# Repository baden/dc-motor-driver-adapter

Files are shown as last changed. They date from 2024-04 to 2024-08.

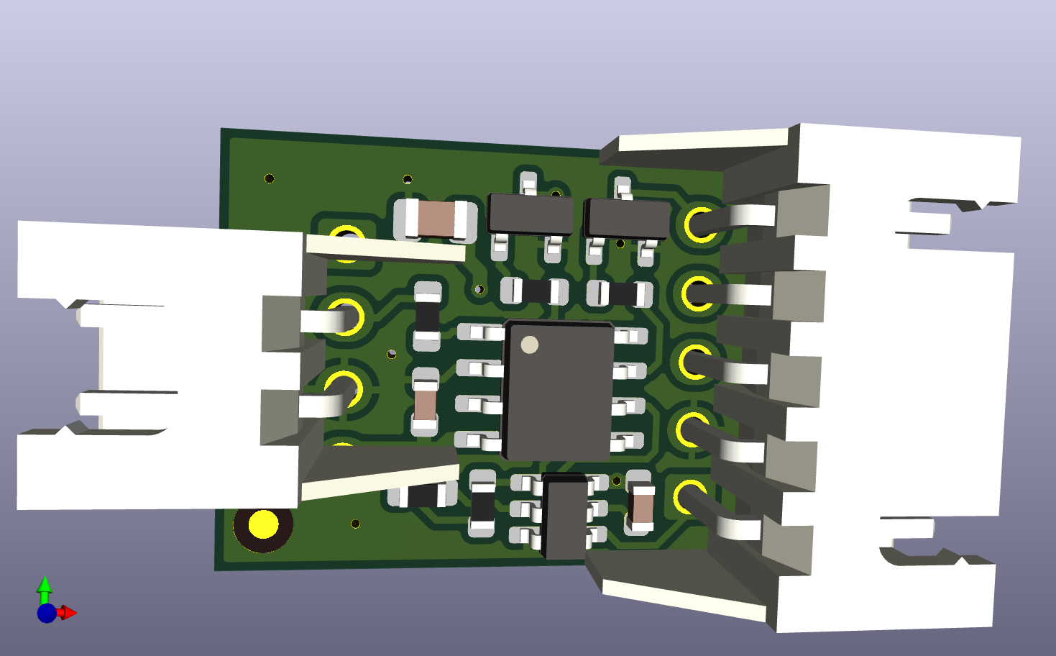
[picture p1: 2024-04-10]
board/revision-3/docs/dc-motor-driver-adapter.png

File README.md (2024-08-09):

# dc-motor-driver-adapter

Тут буде і плата і програма.

## Встановлення інструментів

https://github.com/riscv-software-src/homebrew-riscv

```bash
brew tap riscv-software-src/riscv
brew install riscv-tools
brew install riscv-openocd
brew test riscv-tools
/opt/homebrew/opt/riscv-gnu-toolchain/bin/riscv64-unknown-elf-gcc --version
```

/opt/homebrew/opt/riscv-openocd/bin/openocd

Во, подивиться це:

https://github.com/wagiminator/CH32V003-GameConsole/tree/main

Ще це:
https://github.com/wagiminator/MCU-Templates

Ще тут купа посилань:
https://github.com/wagiminator/Development-Boards/tree/main/CH32V003A4M6_DevBoard

https://github.com/AlessandroAU/ESP32-CRSF-Packet-Gen/blob/master/CRSF_testcode/CRSF.h
https://px4.github.io/Firmware-Doxygen/d9/dd2/crsf_8cpp_source.html

https://github.com/vedderb/bldc_uart_comm_stm32f4_discovery/blob/c19a6283e187040f25aa52e213673938db054d06/bldc_interface.c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

https://vedder.se/2015/10/communicating-with-the-vesc-using-uart/

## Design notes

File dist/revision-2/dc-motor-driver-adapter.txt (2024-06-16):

Name: dc-motor-driver-adapter
Revision: 2

Dimension: 16.0mm x 10.0mm
Thickness: 1.6mm
Layers: 2

Gerber files:

Copper layers (orger from top to bottom):
Top copper:         dc-motor-driver-adapter-F_Cu.gtl
Bottom copper:      dc-motor-driver-adapter-B_Cu.gbl

Top solder mask:    dc-motor-driver-adapter-F_Mask.gts
Bottom solder mask: dc-motor-driver-adapter-B_Mask.gbs
Silkscreen:         dc-motor-driver-adapter-B_Silkscreen.gbo
Outline:            dc-motor-driver-adapter-Edge_Cuts.gm1
Top solder paste:   dc-motor-driver-adapter-F_Paste.gtp
Drill:              dc-motor-driver-adapter.drl

Color of solder mask: green
Silkscreen color: white
Surface Finish: HASL

Copper weight: 1oz

Material details: FR4-Standard Tg 140C

Recomend panelizing: 4x5 vcut

Components positions: dc-motor-driver-adapter-top.pos
Components positions (CSV): dc-motor-driver-adapter-top.pos.csv
Components positions (human pdf): dc-motor-driver-adapter-Top.pdf
Components positions (human pdf): dc-motor-driver-adapter-Bottom.pdf

Components list: dc-motor-driver-adapter.bom.csv

Assembled board example: dc-motor-driver-adapter.png

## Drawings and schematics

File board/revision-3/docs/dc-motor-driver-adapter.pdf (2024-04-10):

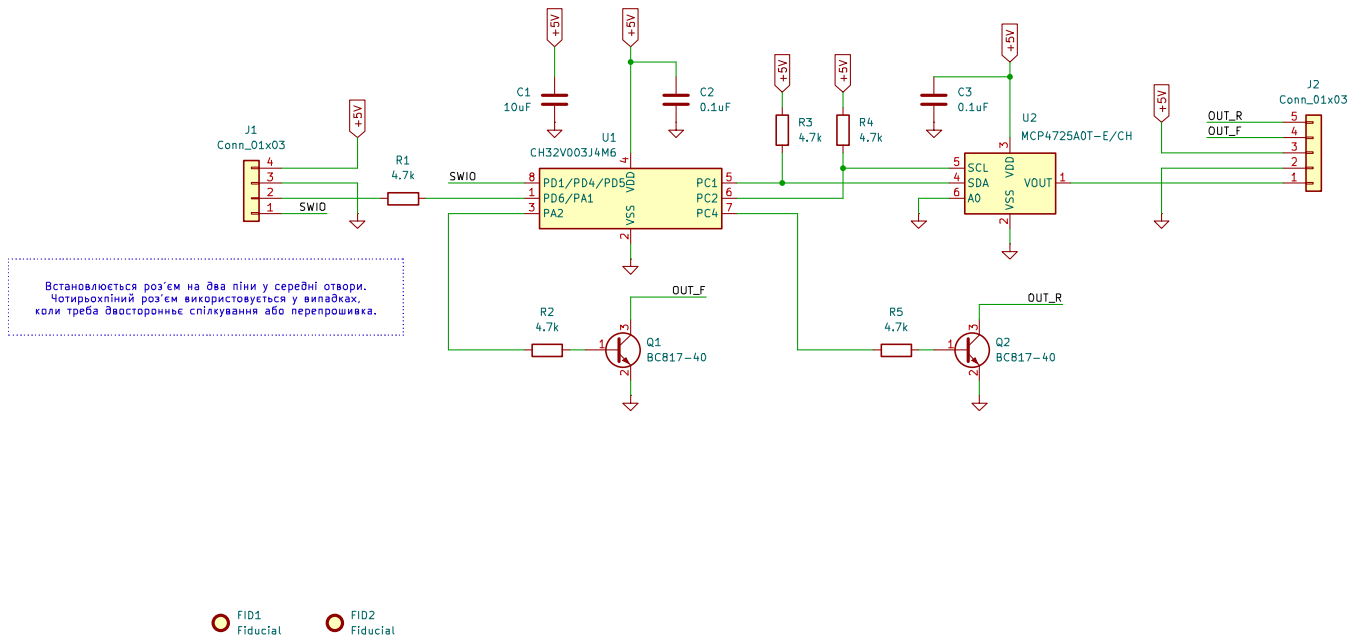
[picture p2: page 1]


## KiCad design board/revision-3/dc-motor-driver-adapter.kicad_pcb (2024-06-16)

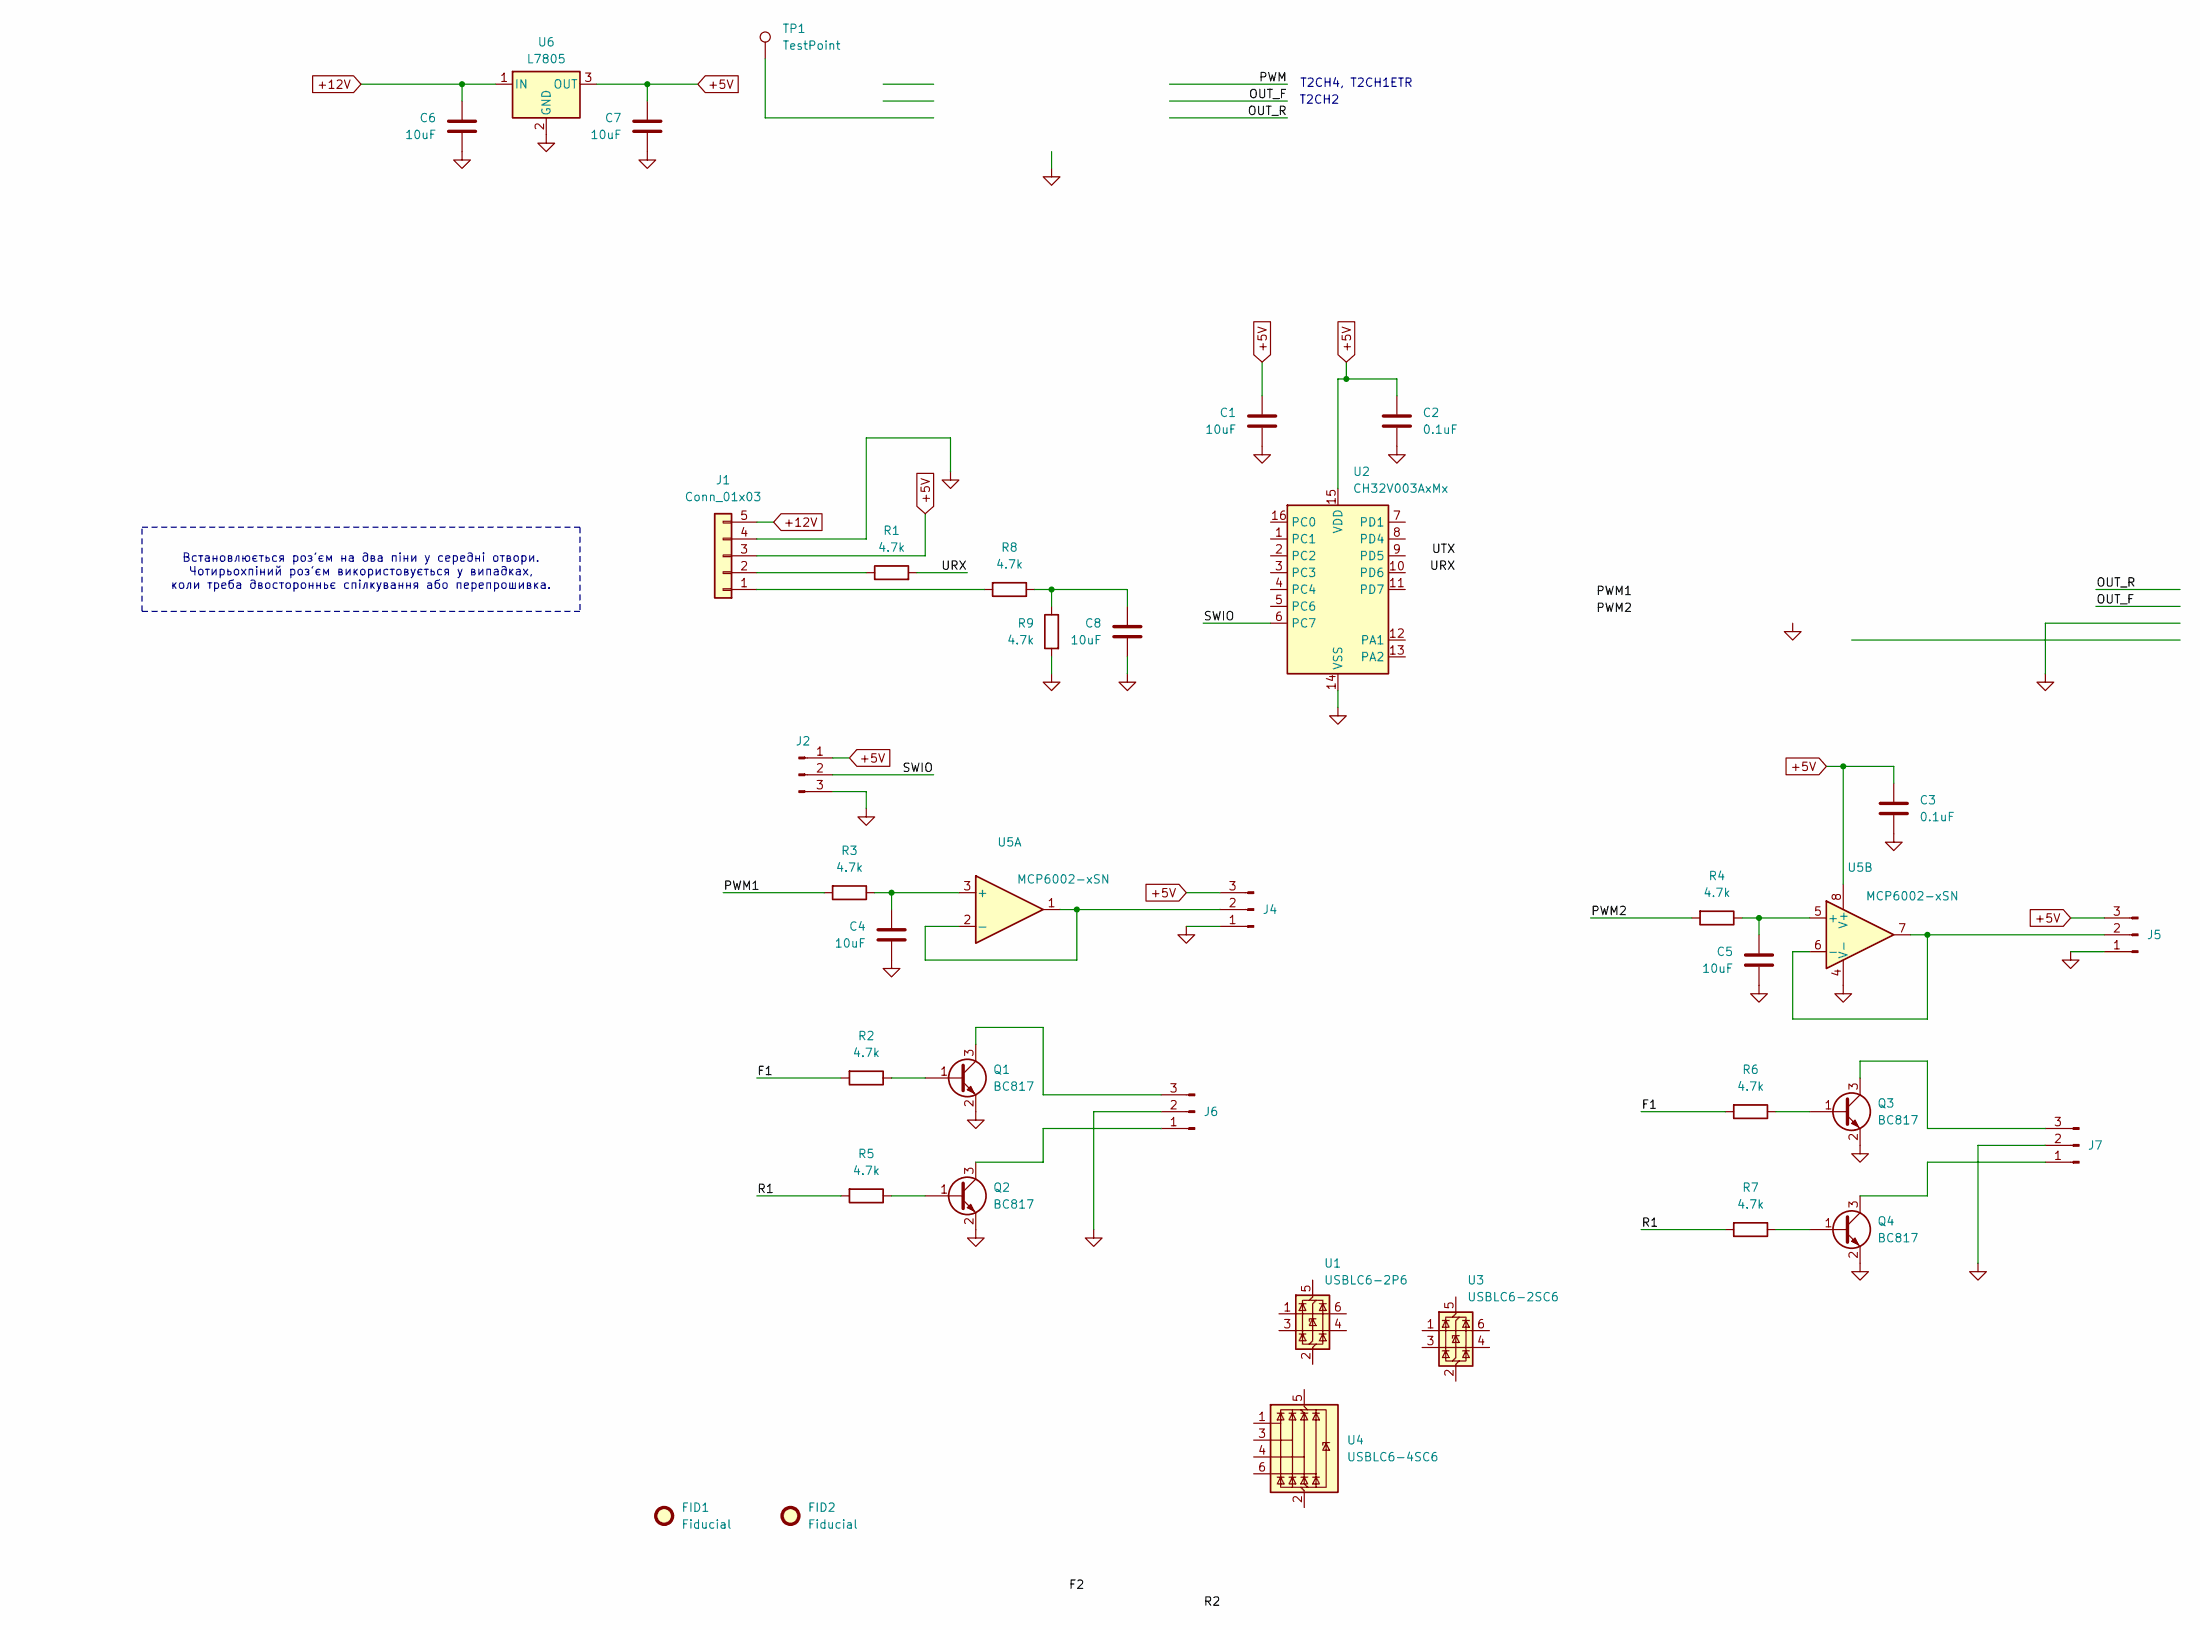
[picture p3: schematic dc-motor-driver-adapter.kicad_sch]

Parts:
C1, C4, C5, C6, C7, C8: 10uF; C_0805_2012Metric
C2, C3: 0.1uF; C_0603_1608Metric
FID1, FID2: Fiducial; Fiducial_1mm_Mask2mm
J1: Conn_01x03; JST_PH_S5B-PH-K_1x05_P2.00mm_Horizontal
J2, J4, J5, J6, J7: Conn_01x03_Pin; JST_PH_B3B-PH-K_1x03_P2.00mm_Vertical
Q1, Q2, Q3, Q4: BC817; SOT-23
R1, R2, R3, R4, R5, R6, R7, R8, R9: 4.7k; R_0603_1608Metric
TP1: TestPoint; TestPoint_Pad_2.0x2.0mm
U1: USBLC6-2P6; SOT-666
U2: CH32V003AxMx; SOP-16_3.9x9.9mm_P1.27mm
U3: USBLC6-2SC6; SOT-23-6
U4: USBLC6-4SC6; SOT-23-6
U5: MCP6002-xSN; SO-8_3.9x4.9mm_P1.27mm
U6: L7805; TO-252-2

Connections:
+5V: C1.1, C2.1, C3.1, C7.1, J1.3, J2.1, J4.3, J5.3, U2.15 (VDD), U5.8 (V+), U6.3 (OUT)
+12V: C6.1, J1.5, U6.1 (IN)
/F1: R2.2, R6.2
/PWM1: R3.2
/PWM2: R4.2
/R1: R5.2, R7.2
/SWIO: J2.2, U2.6 (PC7)
/URX: R1.2
GND: C1.2, C2.2, C3.2, C4.2, C5.2, C6.2, C7.2, C8.2, J1.4, J2.3, J4.1, J5.1, J6.2, J7.2, Q1.2 (E), Q2.2 (E), Q3.2 (E), Q4.2 (E), R9.2, U2.14 (VSS), U5.4 (V-), U6.2 (GND)
unnamed: C8.1, R8.1, R9.1
unnamed: J1.2, R1.1
unnamed: J4.2, U5.1, U5.2 (-)
unnamed: J5.2, U5.6 (-), U5.7
unnamed: J6.1, Q2.3 (C)
unnamed: J6.3, Q1.3 (C)
unnamed: J7.1, Q4.3 (C)
unnamed: J7.3, Q3.3 (C)
unnamed: Q1.1 (B), R2.1
unnamed: Q2.1 (B), R5.1
unnamed: Q3.1 (B), R6.1
unnamed: Q4.1 (B), R7.1
unnamed: J1.1, R8.2
unnamed: C4.1, R3.1, U5.3 (+)
unnamed: C5.1, R4.1, U5.5 (+)

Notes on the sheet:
Встановлюється роз'єм на два піни у середні отвори. Чотирьохпіний роз'єм використовується у випадках, коли треба двосторонньє спілкування або перепрошивка.
T2CH2
T2CH4, T2CH1ETR

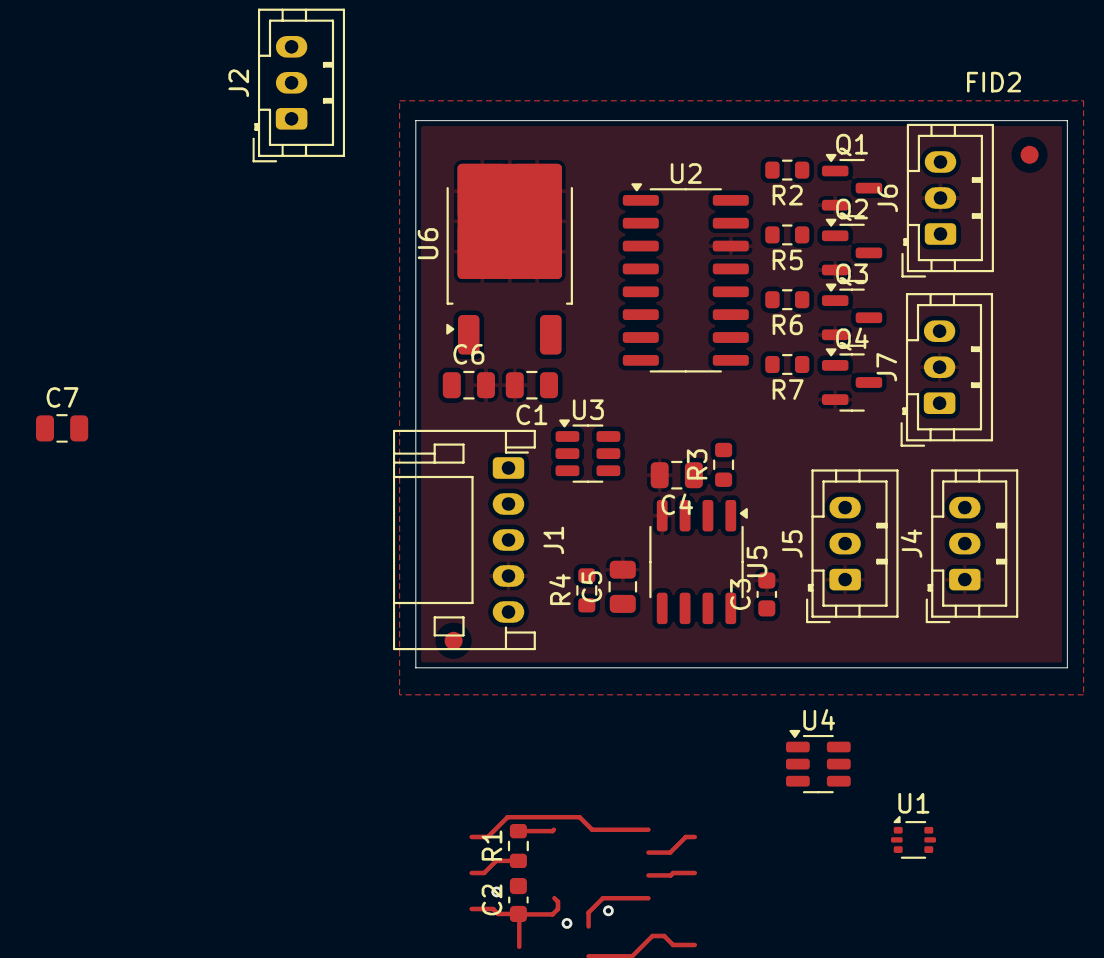
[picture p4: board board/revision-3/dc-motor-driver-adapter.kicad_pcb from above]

Board: 2 copper layers, 36.2 x 30.4 mm, 33 parts (1 on the bottom side), 19 nets.

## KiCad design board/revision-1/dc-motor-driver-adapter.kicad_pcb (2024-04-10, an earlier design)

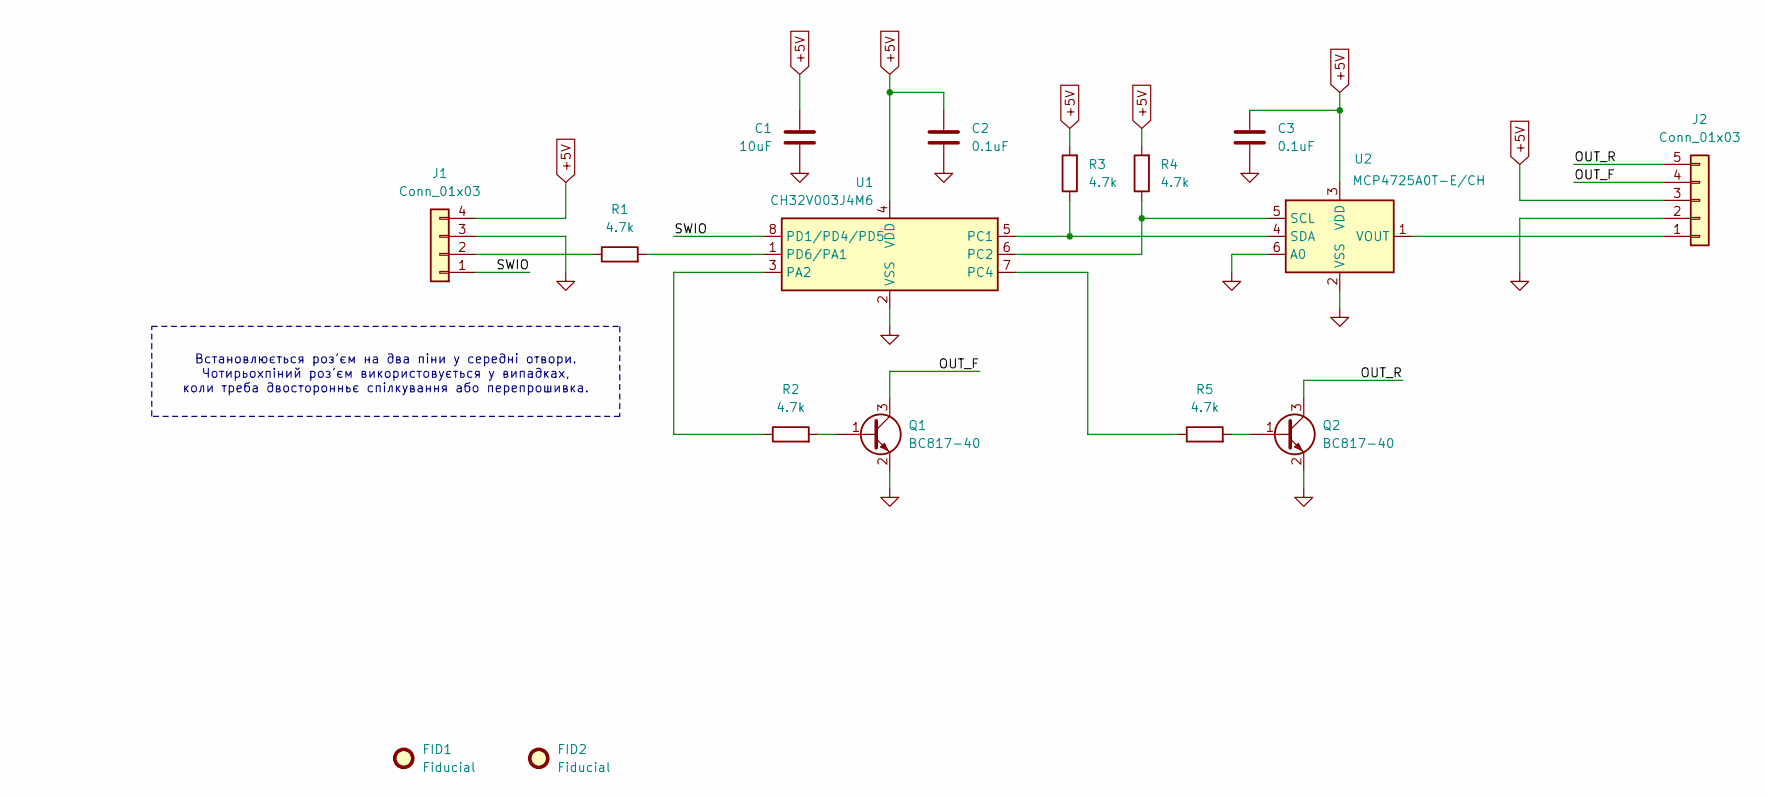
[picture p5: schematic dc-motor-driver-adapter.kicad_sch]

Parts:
C1: 10uF; C_0805_2012Metric
C2, C3: 0.1uF; C_0603_1608Metric
FID1, FID2: Fiducial; Fiducial_1mm_Mask2mm
J1: Conn_01x03; JST_XH_S4B-XH-A-1_1x04_P2.50mm_Horizontal
J2: Conn_01x03; JST_XH_S5B-XH-A-1_1x05_P2.50mm_Horizontal
Q1, Q2: BC817-40; SOT-23
R1, R2, R3, R4, R5: 4.7k; R_0603_1608Metric
U1: CH32V003J4M6; SOP-8_3.9x4.9mm_P1.27mm
U2: MCP4725A0T-E/CH; SOT-23-6

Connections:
+5V: C1.1, C2.1, C3.1, J1.4, J2.3, R3.2, R4.2, U1.4 (VDD), U2.3 (VDD)
/OUT_F: J2.4, Q1.3 (C)
/OUT_R: J2.5, Q2.3 (C)
/SWIO: J1.1, U1.8 (PD1/PD4/PD5)
GND: C1.2, C2.2, C3.2, J1.3, J2.2, Q1.2 (E), Q2.2 (E), U1.2 (VSS), U2.2 (VSS), U2.6 (A0)
unnamed: J1.2, R1.1
unnamed: J2.1, U2.1 (VOUT)
unnamed: Q1.1 (B), R2.2
unnamed: Q2.1 (B), R5.2
unnamed: R2.1, U1.3 (PA2)
unnamed: R3.1, U1.5 (PC1), U2.4 (SDA)
unnamed: R4.1, U1.6 (PC2), U2.5 (SCL)
unnamed: R5.1, U1.7 (PC4)
unnamed: R1.2, U1.1 (PD6/PA1)

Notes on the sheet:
Встановлюється роз'єм на два піни у середні отвори. Чотирьохпіний роз'єм використовується у випадках, коли треба двосторонньє спілкування або перепрошивка.

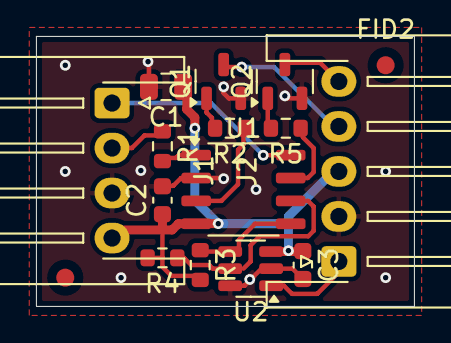
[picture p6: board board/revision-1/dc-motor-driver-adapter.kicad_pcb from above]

Board: 2 copper layers, 21.0 x 15.0 mm, 16 parts (0 on the bottom side), 14 nets.

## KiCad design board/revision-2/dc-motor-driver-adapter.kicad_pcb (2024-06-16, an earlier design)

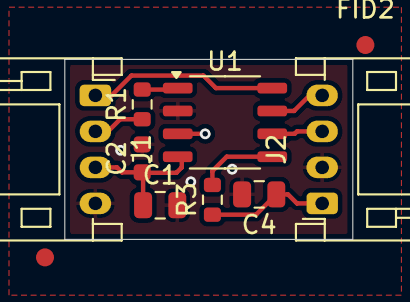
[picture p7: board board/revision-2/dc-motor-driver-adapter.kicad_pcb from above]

Board: 2 copper layers, 16.0 x 10.0 mm, 11 parts (1 on the bottom side), 10 nets.

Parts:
C1, C4: 10uF; C_0805_2012Metric
C2: 0.1uF; C_0603_1608Metric
FID1, FID2: Fiducial; Fiducial_1mm_Mask2mm
J1, J2: Conn_01x03; JST_PH_S4B-PH-K_1x04_P2.00mm_Horizontal
R1, R3: 4.7k; R_0603_1608Metric
TP1: TestPoint; TestPoint_Pad_2.0x2.0mm
U1: CH32V003J4M6; SOP-8_3.9x4.9mm_P1.27mm

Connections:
+5V: C1.1, C2.1, J1.3, U1.4 (VDD)
/OUT_F: J2.3, U1.6 (PC2)
/OUT_R: J2.4, U1.7 (PC4)
/PWM: R3.2, U1.5 (PC1)
/SWIO: J1.1, U1.8 (PD1/PD4/PD5)
/URX: R1.2, U1.1 (PD6/PA1)
GND: C1.2, C2.2, C4.2, J1.4, J2.2, U1.2 (VSS)
unnamed: J1.2, R1.1
unnamed: C4.1, J2.1, R3.1
unnamed: TP1.1, U1.3 (PA2)

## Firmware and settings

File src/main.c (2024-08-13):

#include <stdbool.h>
#include "gpio.h"
#include "debug_serial.h"
#include "uart_rx.h"
#include "crsf.h"
#include "dac.h"
#include "system.h"


// Device modes:
// 1 - Керування лебідкою по каналу 12
// 2 - Керування лівим бортом по каналах 1 та 2  (1+2)
// 3 - Керування правим бортом по каналах 1 та 2 (2-1)

#if !defined(DEVICE_MODE)
    #error "DEVICE_MODE is not defined"
#endif
// #define DEVICE_MODE 3

// Керування тільки аналоговим виходом з нулем у середині діапазону
#define DEVICE_ANALOG_ONLY 1

//#define STARTKIT 1

#if defined(STARTKIT)

    #define PIN_LED    PD0   // pin connected to LED (Startkit)

#else

#endif


static inline void init(void)
{
    #if defined(STARTKIT)
        PIN_output(PIN_LED);
        PIN_high(PIN_LED);

        PIN_output(PC0);   // "+" for LED
        PIN_high(PC0);
    #endif

    #if 0
    PIN_input_PD(PD6); // Вхід для PPM (UART) (підтягнутий до землі)
    #endif

    // SYS_init();
    UART_init();
    dac_init();

    #if DEVICE_MODE == 1
        dac_write(2730);        // TODO: Підібрати напругу 12В
    #else
        #if defined(DEVICE_ANALOG_ONLY) && (DEVICE_ANALOG_ONLY == 1)
            dac_write(2047);    // За замовчуванням напруга 1/2
        #else
            dac_write(4095);
        #endif
    #endif

#if 0
    // Configure PD6 as interrupt input
    // The "port" is:
    // 0 for Port A
    // 1 for Port B
    // 2 for Port C
    // 3 for Port D
    #define _portno 3
    #define _pin 6

    RCC->APB2PCENR |= RCC_AFIOEN;
	// Configure the IO as an interrupt.
    AFIO->EXTICR = _portno << (_pin * 2);
	EXTI->INTENR = EXTI_INTENR_MR6; // Enable EXT6
	EXTI->RTENR = EXTI_RTENR_TR6;  // Rising edge trigger
    EXTI->FTENR = EXTI_FTENR_TR6;  // Falling edge trigger

    // enable pin-change-interrupt.
    NVIC_EnableIRQ( EXTI7_0_IRQn );
#endif

#if 0
    RCC->APB2PCENR |= RCC_TIM1EN; // enable TIM1 clock
    // RCC->APB2PRSTR = RCC_TIM1RST;
	// RCC->APB2PRSTR = 0;

	TIM1->ATRLR = 0xffff;
	TIM1->PSC = 47; // 48MHz/(47+1) -> 1µs resolution

    // D2 Capture Input(T1CH1)
    // PA1 - T1CH2

	TIM1->CHCTLR1 = TIM_CC1S_0 | TIM_CC2S_1;

	TIM1->CCER = TIM_CC1E|TIM_CC2E|TIM_CC2P;

	TIM1->CTLR1 = TIM_CEN;

	NVIC_EnableIRQ(TIM1_CC_IRQn);
	TIM1->DMAINTENR = TIM_CC1IE|TIM_CC2IE;    
#endif

//   ADC_init();
//   ADC_input(PIN_PAD);

    // DEBUG_init();
}

#if 0
volatile unsigned int counter = 0;
volatile uint32_t last_value = 0;

void EXTI7_0_IRQHandler( void ) __attribute__((interrupt));
void EXTI7_0_IRQHandler( void ) 
{
    static uint32_t starttime;

    PIN_high(PC1);
    unsigned pin = PIN_read(PD6);

    if(pin != 0) {
        starttime = STK->CNT;
    } else {
        last_value = STK->CNT - starttime;
    }
	EXTI->INTFR = EXTI_INTF_INTF6;
    PIN_low(PC1);
}
#endif

#if DEVICE_MODE == 1

static void rxTo(int val)
{
    if(val < 500) {
        #if defined(STARTKIT)
            PIN_low(PIN_LED);
        #endif
        PIN_high(PC4);
        PIN_low(PA2);
    } else if(val > 1500) {
        #if defined(STARTKIT)
            PIN_low(PIN_LED);
        #endif
        PIN_low(PC4);
        PIN_high(PA2);
    } else {
        #if defined(STARTKIT)
            PIN_high(PIN_LED);
        #endif
        PIN_low(PC4);
        PIN_low(PA2);
    }
}

static void rxFoo()
{
    int val = channel[12 -1];

    // Middle = 1044
    // Low = 191
    // High = 1792
    rxTo(val);
}

#elif (DEVICE_MODE == 2) || (DEVICE_MODE == 3) 

#define LOW_PASS_FILTER
// CRSF center value is 992
#define CENTER_X 992
#define CENTER_Y 992
#define MAX_X 820
#define MAX_Y 820
#define DEAD_ZONE 10

static void rxTo(int dac_val)
{
    #ifdef LOW_PASS_FILTER
        static int last_dac_val = 0;
        int _dac = dac_val;
        dac_val = (dac_val + last_dac_val) / 2;
        last_dac_val = _dac;
    #endif

    if((dac_val < DEAD_ZONE) && (dac_val > -DEAD_ZONE)) {
        #if defined(DEVICE_ANALOG_ONLY) && (DEVICE_ANALOG_ONLY == 1)
            dac_write(2047);
        #else
            dac_write(4095);
            PIN_low(PC4);
            PIN_low(PA2);
        #endif
    } else {
        #if defined(DEVICE_ANALOG_ONLY) && (DEVICE_ANALOG_ONLY == 1)
            dac_val *= 5; // (channel[3 -1] - 1000) * 4096 / 1000;
            dac_val += 2048;
            if(dac_val < 0) {
                dac_val = 0;
            } else if(dac_val > 4095) {
                dac_val = 4095;
            }
            dac_write(dac_val);
        #else
            if(dac_val > 0) {
                PIN_low(PC4);
                PIN_high(PA2);
            } else {
                PIN_low(PA2);
                PIN_high(PC4);
                dac_val = -dac_val;
            }

            dac_val *= 5; // (channel[3 -1] - 1000) * 4096 / 1000;
            if(dac_val < 0) {
                dac_val = 0;
            } else if(dac_val > 4095) {
                dac_val = 4095;
            }
            dac_write(4095-dac_val);

        #endif

    }
}

static void rxFoo()
{
    // bool in_dead_zone = false;

    int X = channel[1 -1] - CENTER_X;   // -MAX_X to MAX_X
    int Y = channel[2 -1] - CENTER_Y;   // -MAX_Y to MAX_Y

    #if (DEVICE_MODE == 2)
        int dac_val = (X+Y);
    #else
        int dac_val = (Y-X);
    #endif
    rxTo(dac_val);
}

#endif

int main(void)
{
    // PIN_output(PC1);

    PIN_output(PC4);    // Right
    PIN_low(PC4);
    PIN_output(PA2);    // Left
    PIN_low(PA2);

    init();

    #if defined(STARTKIT)
        PIN_low(PIN_LED);
    #endif

    // DEBUG_println("Start");

    #define RX_TIMEOUT  500 * DLY_MS_TIME

    uint32_t next_tick = STK->CNT + RX_TIMEOUT;

//   while(((int32_t)(STK->CNT - end)) < 0);


    while(1)
    {
        // #if defined(STARTKIT)
        //     PIN_toggle(PIN_LED);
        // #endif
        // DLY_ms(500);

        if(UART_available()) {
            char c = USART1->DATAR;
            rxParseByte(c);
            // PIN_toggle(PIN_LED);

            if(crsf_frame_ready) {
                crsf_frame_ready = false;
                rxFoo();
                next_tick = STK->CNT + RX_TIMEOUT;
            }
        }

        if(((int32_t)(STK->CNT - next_tick)) > 0) {
            next_tick = STK->CNT + RX_TIMEOUT;

            #if DEVICE_MODE == 1
                rxTo(1000);
            #else
                rxTo(0);
            #endif
            // next_tick += 1000 * DLY_MS_TIME;
        // //     // dac_write(0);

        //     PIN_toggle(PC4);
        // //     // PIN_high(PC4);

        }

    #if 0
        counter++;
        uint32_t duration = last_value / (F_CPU / 1000000);        // Значення у мікросекундах

        DEBUG_printf("Counter: %d  Last value: %d  Duration: %d\n", counter, last_value, duration);
    #endif
    }
}

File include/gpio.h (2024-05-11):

// ===================================================================================
// Basic GPIO Functions for CH32V003                                          * v1.5 *
// ===================================================================================
//
// Pins must be defined as PA0, PA1, .., PC0, PC1, etc. - e.g.:
// #define PIN_LED PC0      // LED on pin PC0
//
// PIN functions available:
// ------------------------
// PIN_input(PIN)           Set PIN as INPUT (floating, no pullup/pulldown)
// PIN_input_PU(PIN)        Set PIN as INPUT with internal PULLUP resistor
// PIN_input_PD(PIN)        Set PIN as INPUT with internal PULLDOWN resistor
// PIN_input_AN(PIN)        Set PIN as INPUT for analog peripherals (e.g. ADC) (*)
// PIN_output(PIN)          Set PIN as OUTPUT (push-pull)
// PIN_output_OD(PIN)       Set PIN as OUTPUT (open-drain)
// PIN_alternate(PIN)       Set PIN as alternate output (push-pull)
// PIN_alternate_OD(PIN)    Set PIN as alternate output (open-drain)
//
// PIN_low(PIN)             Set PIN output value to LOW (*)
// PIN_high(PIN)            Set PIN output value to HIGH
// PIN_toggle(PIN)          TOGGLE PIN output value
// PIN_read(PIN)            Read PIN input value
// PIN_write(PIN, val)      Write PIN output value (0 = LOW / 1 = HIGH)
//
// PORT functions available:
// -------------------------
// PORT_enable(PIN)         Enable GPIO PORT of PIN
// PORTA_enable()           Enable GPIO PORT A
// PORTC_enable()           Enable GPIO PORT C
// PORTD_enable()           Enable GPIO PORT D
// PORTS_enable()           Enable all GPIO PORTS
//
// PORT_disable(PIN)        Disable GPIO PORT of PIN
// PORTA_disable()          Disable GPIO PORT A
// PORTC_disable()          Disable GPIO PORT C
// PORTD_disable()          Disable GPIO PORT D
// PORTS_disable()          Disable all GPIO PORTS
//
// Analog-to-Digital Converter (ADC) functions available:
// ------------------------------------------------------
// ADC_init()               Init, enable and calibrate ADC (must be called first)
// ADC_enable()             Enable ADC (power-up)
// ADC_disable()            Disable ADC (power-down)
// ADC_calibrate()          Calibrate ADC
//
// ADC_fast()               Set fast mode   ( 28 clock cycles, least accurate) (*)
// ADC_medium()             Set medium mode (168 clock cycles, medium accurate)
// ADC_slow()               Set slow mode   (504 clock cycles, most accurate)
//
// ADC_input(PIN)           Set PIN as ADC input
// ADC_input_VREF()         Set internal voltage referece (Vref) as ADC input
// ADC_input_VCAL()         Set calibration voltage (Vcal) as ADC input
//
// ADC_read()               Sample and read ADC value (0..1023)
// ADC_read_VDD()           Sample and read supply voltage (VDD) in millivolts (mV)
//
// Op-Amp Comparator (OPA) functions available:
// --------------------------------------------
// OPA_enable()             Enable OPA comparator
// OPA_disable()            Disable OPA comparator
// OPA_negative(PIN)        Set OPA inverting input PIN (PA1, PD0 only)
// OPA_positive(PIN)        Set OPA non-inverting input PIN (PA2, PD7 only)
// OPA_output()             Enable OPA output (push-pull) on pin PD4
// OPA_output_OD()          Enable OPA output (open-drain) on pin PD4
// OPA_read()               Read OPA output (0: pos < neg, 1: pos > neg)
//
// Notes:
// ------
// - (*) default state
// - Pins used for ADC must be set with PIN_input_AN beforehand. Only the following 
//   pins can be used as INPUT for the ADC: PA1, PA2, PC4, PD2, PD3, PD4, PD5, PD6.
// - Pins used as input for OPA comparator must be set with PIN_input_AN beforehand.
//   Only the following pins can be used for the OPA: PA1 or PD0 as negative
//   (inverting) input, PA2 or PD7 as positive (non-inverting) input and PD4 as
//   ouput.
//
// 2023 by Stefan Wagner:   https://github.com/wagiminator

#pragma once

#ifdef __cplusplus
extern "C" {
#endif

#include "system.h"

// ===================================================================================
// Enumerate PIN designators (use these designators to define pins)
// ===================================================================================
enum{ PA0, PA1, PA2, PA3, PA4, PA5, PA6, PA7,
      PC0, PC1, PC2, PC3, PC4, PC5, PC6, PC7,
      PD0, PD1, PD2, PD3, PD4, PD5, PD6, PD7};
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

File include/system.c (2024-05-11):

// ===================================================================================
// Basic System Functions for CH32V003                                        * v1.5 *
// ===================================================================================
//
// This file must be included!!!!
//
// References:
// -----------
// - CNLohr ch32v003fun: https://github.com/cnlohr/ch32v003fun
// - WCH Nanjing Qinheng Microelectronics: http://wch.cn
//
// 2023 by Stefan Wagner:   https://github.com/wagiminator

#include "system.h"

// ===================================================================================
// Setup Microcontroller (this function is called automatically at startup)
// ===================================================================================
void SYS_init(void) {
  // Init system clock
  #if SYS_CLK_INIT > 0
  #if F_CPU > 24000000
  FLASH->ACTLR = FLASH_ACTLR_LATENCY_1;                     // 1 cycle latency
  #endif
  CLK_init();                                               // init system clock
  #endif

  // Init SYSTICK
  #if SYS_TICK_INIT > 0
  STK_init();
  #endif

  // Enable GPIO
  #if SYS_GPIO_EN > 0
    RCC->APB2PCENR |= RCC_IOPAEN | RCC_IOPCEN | RCC_IOPDEN;
  #endif
}

// ===================================================================================
// System Clock Functions
// ===================================================================================

// Init internal oscillator (non PLL) as system clock source
void CLK_init_HSI(void) {
  RCC->CFGR0 = CLK_DIV;                                         // set clock divider
}

// Init internal oscillator with PLL as system clock source
void CLK_init_HSI_PLL(void) {
  RCC->CTLR  = RCC_HSION | RCC_PLLON | ((HSITRIM) << 3);        // enable PLL, keep HSI on
  while(!(RCC->CTLR & RCC_PLLRDY));                             // wait till PLL is ready
  RCC->CFGR0 = CLK_DIV | RCC_SW_PLL;                            // select PLL as system clock source
  while((RCC->CFGR0 & RCC_SWS) != RCC_SWS_PLL);                 // wait till PLL is used as system clock source
}

// Init external crystal (non PLL) as system clock source
void CLK_init_HSE(void) {
  RCC->APB2PCENR |= RCC_AFIOEN;                                 // enable auxiliary clock module
  AFIO->PCFR1    |= AFIO_PCFR1_PA12_REMAP;                      // pins PA1-PA2 for external crystal
  RCC->CTLR       = RCC_HSION | RCC_HSEON | ((HSITRIM) << 3);   // enable HSE and keep HSI on
  while(!(RCC->CTLR & RCC_HSERDY));                             // wait till HSE is ready
  RCC->CFGR0      = CLK_DIV | RCC_SW_HSE;                       // set clock divider, use HSE for system clock
  while((RCC->CFGR0 & RCC_SWS) != RCC_SWS_HSE);                 // wait till HSE is used as system clock source
}

// Init external crystal (PLL) as system clock source
void CLK_init_HSE_PLL(void) {
  RCC->APB2PCENR |= RCC_AFIOEN;                                 // enable auxiliary clock module
  AFIO->PCFR1    |= AFIO_PCFR1_PA12_REMAP;                      // pins PA1-PA2 for external crystal
  RCC->CTLR       = RCC_HSION | RCC_HSEON | ((HSITRIM) << 3);   // enable HSE and keep HSI on
  while(!(RCC->CTLR & RCC_HSERDY));                             // wait till HSE is ready
  RCC->CFGR0      = RCC_PLLSRC | CLK_DIV;                       // set clock divider, use HSE as PLL source
  RCC->CTLR       = RCC_PLLON | RCC_HSION | RCC_HSEON | ((HSITRIM) << 3);   // enable PLL
  while(!(RCC->CTLR & RCC_PLLRDY));                             // wait till PLL is ready
  RCC->CFGR0      = RCC_PLLSRC | CLK_DIV | RCC_SW_PLL;          // select PLL as system clock source
  while((RCC->CFGR0 & RCC_SWS) != RCC_SWS_PLL);                 // wait till PLL is used as system clock source
}

// Reset system clock to default state
void CLK_reset(void) {
  RCC->CTLR |= RCC_HSION;                                       // enable HSI
  while(!(RCC->CTLR & RCC_HSIRDY));                             // wait until HSI is ready
  RCC->CFGR0 = 0x00000000;                                      // select HSI as system clock source
  while(RCC->CFGR0 & RCC_SWS);                                  // wait until HSI is selected
  RCC->CTLR  = RCC_HSION | ((HSITRIM) << 3);                    // use HSI only
  RCC->INTR  = 0x009F0000;                                      // disable interrupts and clear flags
  FLASH->ACTLR = FLASH_ACTLR_LATENCY_0;                         // no flash wait states
}

// Setup pin PC4 for MCO (output, push-pull, 50MHz, auxiliary)
void MCO_init(void) {
  RCC->APB2PCENR |= RCC_AFIOEN | RCC_IOPCEN;
  GPIOC->CFGLR    = (GPIOC->CFGLR & ~((uint32_t)0b1111<<(4<<2))) | ((uint32_t)0b1011<<(4<<2));
}

// ===================================================================================
// Delay Functions
// ===================================================================================

// Wait n counts of SysTick
void DLY_ticks(uint32_t n) {
  uint32_t end = STK->CNT + n;
  while(((int32_t)(STK->CNT - end)) < 0);
}

// ===================================================================================
// Independent Watchdog Timer (IWDG) Functions
// ===================================================================================

// Start independent watchdog timer (IWDG) with given time in milliseconds (max 8191).
// Once the IWDG has been started, it cannot be disabled, only reloaded (feed).
// It can be stopped by disabling the internal low-speed clock (LSI).
void IWDG_start(uint16_t ms) {
  LSI_enable();                         // enable internal low-speed clock (LSI)
  IWDG->CTLR = 0x5555;                  // allow register modification
  while(IWDG->STATR & IWDG_PVU);        // wait for clock register to be ready
  IWDG->PSCR = 0b111;                   // set LSI clock prescaler 256
  while(IWDG->STATR & IWDG_RVU);        // wait for reload register to be ready
  IWDG->RLDR = ms >> 1;                 // set watchdog counter reload value
  IWDG->CTLR = 0xAAAA;                  // load reload value into watchdog counter
  IWDG->CTLR = 0xCCCC;                  // enable IWDG
}

// Reload watchdog counter with n milliseconds, n<=8191
void IWDG_reload(uint16_t ms) {
  IWDG->CTLR = 0x5555;                  // allow register modification
  while(IWDG->STATR & IWDG_RVU);        // wait for reload register to be ready
  IWDG->RLDR = ms >> 1;                 // set watchdog counter reload value
  IWDG->CTLR = 0xAAAA;                  // load reload value into watchdog counter
}

// ===================================================================================
// Automatic Wake-up Timer (AWU) Functions
// ===================================================================================
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

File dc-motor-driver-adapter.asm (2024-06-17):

dc-motor-driver-adapter.elf:     file format elf32-littleriscv


Disassembly of section .init:

00000000 <jump_reset>:
   0:	3e60006f          	j	3e6 <reset_handler>

00000004 <vectors>:
   4:	00000000 000003e4 000003e4 00000000     ................
	...
  30:	000003e4 00000000 000003e4 00000000     ................
  40:	000003e4 000003e4 000003e4 000003e4     ................
  50:	000003e4 000003e4 000003e4 000003e4     ................
  60:	000003e4 000003e4 000003e4 000003e4     ................
  70:	000003e4 000003e4 000003e4 000003e4     ................
  80:	000003e4 000003e4 000003e4 000003e4     ................
  90:	000003e4 000003e4 000003e4              ............

Disassembly of section .text:

0000009c <SYS_init>:
  9c:	400217b7          	lui	a5,0x40021
  a0:	07000713          	li	a4,112
  a4:	c3d8                	sw	a4,4(a5)
  a6:	4695                	li	a3,5
  a8:	e000f737          	lui	a4,0xe000f
  ac:	c314                	sw	a3,0(a4)
  ae:	4f98                	lw	a4,24(a5)
  b0:	03476713          	or	a4,a4,52
  b4:	cf98                	sw	a4,24(a5)
  b6:	8082                	ret

000000b8 <main>:
  b8:	1151                	add	sp,sp,-12
  ba:	c222                	sw	s0,4(sp)
  bc:	40011437          	lui	s0,0x40011
  c0:	401c                	lw	a5,0(s0)
  c2:	fff10737          	lui	a4,0xfff10
  c6:	177d                	add	a4,a4,-1 # fff0ffff <__global_pointer$+0xdff0f7ff>
  c8:	8ff9                	and	a5,a5,a4
  ca:	6741                	lui	a4,0x10
  cc:	c406                	sw	ra,8(sp)
  ce:	c026                	sw	s1,0(sp)
  d0:	8fd9                	or	a5,a5,a4
  d2:	40011737          	lui	a4,0x40011
  d6:	80070713          	add	a4,a4,-2048 # 40010800 <__global_pointer$+0x20010000>
  da:	c01c                	sw	a5,0(s0)
  dc:	431c                	lw	a5,0(a4)
  de:	76fd                	lui	a3,0xfffff
  e0:	0ff68693          	add	a3,a3,255 # fffff0ff <__global_pointer$+0xdfffe8ff>
  e4:	8ff5                	and	a5,a5,a3
  e6:	1007e793          	or	a5,a5,256
  ea:	c31c                	sw	a5,0(a4)
  ec:	3f45                	jal	9c <SYS_init>
  ee:	400217b7          	lui	a5,0x40021
  f2:	4f98                	lw	a4,24(a5)
  f4:	6691                	lui	a3,0x4
  f6:	02168693          	add	a3,a3,33 # 4021 <uart_rx.c.26d07654+0x2c7d>
  fa:	8f55                	or	a4,a4,a3
  fc:	cf98                	sw	a4,24(a5)
  fe:	40011737          	lui	a4,0x40011
 102:	40070713          	add	a4,a4,1024 # 40011400 <__global_pointer$+0x20010c00>
 106:	4314                	lw	a3,0(a4)
 108:	f1000637          	lui	a2,0xf1000
 10c:	167d                	add	a2,a2,-1 # f0ffffff <__global_pointer$+0xd0fff7ff>
 10e:	8ef1                	and	a3,a3,a2
 110:	08000637          	lui	a2,0x8000
 114:	8ed1                	or	a3,a3,a2
 116:	c314                	sw	a3,0(a4)
 118:	04000693          	li	a3,64
 11c:	cb14                	sw	a3,16(a4)
 11e:	40014737          	lui	a4,0x40014
 122:	09c00693          	li	a3,156
 126:	80d71423          	sh	a3,-2040(a4) # 40013808 <__global_pointer$+0x20013008>
 12a:	6689                	lui	a3,0x2
 12c:	0691                	add	a3,a3,4 # 2004 <uart_rx.c.26d07654+0xc60>
 12e:	80d71623          	sh	a3,-2036(a4)
 132:	4f98                	lw	a4,24(a5)
 134:	002006b7          	lui	a3,0x200
 138:	01176713          	or	a4,a4,17
 13c:	cf98                	sw	a4,24(a5)
 13e:	4fd8                	lw	a4,28(a5)
 140:	8f55                	or	a4,a4,a3
 142:	cfd8                	sw	a4,28(a5)
 144:	401c                	lw	a5,0(s0)
 146:	777d                	lui	a4,0xfffff
 148:	073d                	add	a4,a4,15 # fffff00f <__global_pointer$+0xdfffe80f>
 14a:	8ff9                	and	a5,a5,a4
 14c:	6705                	lui	a4,0x1
 14e:	dd070713          	add	a4,a4,-560 # dd0 <system.c.06ca16bb+0x17e>
 152:	8fd9                	or	a5,a5,a4
 154:	c01c                	sw	a5,0(s0)
 156:	400057b7          	lui	a5,0x40005
 15a:	40078793          	add	a5,a5,1024 # 40005400 <__global_pointer$+0x20004c00>
 15e:	4711                	li	a4,4
 160:	00e79223          	sh	a4,4(a5)
 164:	7761                	lui	a4,0xffff8
 166:	0729                	add	a4,a4,10 # ffff800a <__global_pointer$+0xdfff780a>
 168:	00e79e23          	sh	a4,28(a5)
 16c:	4705                	li	a4,1
 16e:	00e79023          	sh	a4,0(a5)
 172:	0187d703          	lhu	a4,24(a5)
 176:	8b09                	and	a4,a4,2
 178:	ff6d                	bnez	a4,172 <main+0xba>
 17a:	0007d703          	lhu	a4,0(a5)
 17e:	10076713          	or	a4,a4,256
 182:	00e79023          	sh	a4,0(a5)
 186:	400057b7          	lui	a5,0x40005
 18a:	40078793          	add	a5,a5,1024 # 40005400 <__global_pointer$+0x20004c00>
 18e:	0147d703          	lhu	a4,20(a5)
 192:	8b05                	and	a4,a4,1
 194:	df6d                	beqz	a4,18e <main+0xd6>
 196:	0c000713          	li	a4,192
 19a:	00e79823          	sh	a4,16(a5)
 19e:	400056b7          	lui	a3,0x40005
 1a2:	00820737          	lui	a4,0x820
 1a6:	40068693          	add	a3,a3,1024 # 40005400 <__global_pointer$+0x20004c00>
 1aa:	070d                	add	a4,a4,3 # 820003 <uart_rx.c.26d07654+0x81ec5f>
 1ac:	0146d783          	lhu	a5,20(a3)
 1b0:	0186d603          	lhu	a2,24(a3)
 1b4:	07c2                	sll	a5,a5,0x10
 1b6:	8fd1                	or	a5,a5,a2
 1b8:	8ff9                	and	a5,a5,a4
 1ba:	fee799e3          	bne	a5,a4,1ac <main+0xf4>
 1be:	400057b7          	lui	a5,0x40005
 1c2:	40078793          	add	a5,a5,1024 # 40005400 <__global_pointer$+0x20004c00>
 1c6:	0147d703          	lhu	a4,20(a5)
 1ca:	08077713          	and	a4,a4,128
 1ce:	df65                	beqz	a4,1c6 <main+0x10e>
 1d0:	00079823          	sh	zero,16(a5)
 1d4:	400057b7          	lui	a5,0x40005
 1d8:	40078793          	add	a5,a5,1024 # 40005400 <__global_pointer$+0x20004c00>
 1dc:	0147d703          	lhu	a4,20(a5)
 1e0:	08077713          	and	a4,a4,128
 1e4:	df65                	beqz	a4,1dc <main+0x124>
 1e6:	00079823          	sh	zero,16(a5)
 1ea:	400057b7          	lui	a5,0x40005
 1ee:	40078793          	add	a5,a5,1024 # 40005400 <__global_pointer$+0x20004c00>
 1f2:	0147d703          	lhu	a4,20(a5)
 1f6:	8b11                	and	a4,a4,4
 1f8:	df6d                	beqz	a4,1f2 <main+0x13a>
 1fa:	0007d703          	lhu	a4,0(a5)
 1fe:	20076713          	or	a4,a4,512
 202:	00e79023          	sh	a4,0(a5)
 206:	e000f7b7          	lui	a5,0xe000f
 20a:	4794                	lw	a3,8(a5)
 20c:	002dc7b7          	lui	a5,0x2dc
 210:	6c078793          	add	a5,a5,1728 # 2dc6c0 <uart_rx.c.26d07654+0x2db31c>
 214:	96be                	add	a3,a3,a5
 216:	81018793          	add	a5,gp,-2032 # 20000010 <crsf_payload.0>
 21a:	200000b7          	lui	ra,0x20000
 21e:	400145b7          	lui	a1,0x40014
 222:	80058593          	add	a1,a1,-2048 # 40013800 <__global_pointer$+0x20013000>
 226:	e000f4b7          	lui	s1,0xe000f
 22a:	0005d703          	lhu	a4,0(a1)
 22e:	02077713          	and	a4,a4,32
 232:	18070363          	beqz	a4,3b8 <main.c.f1b9d4c6+0x141>
 236:	0045d703          	lhu	a4,4(a1)
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

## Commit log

2024-04-09 Initial commit.
    [dc-motor-driver-adapter.csv, dc-motor-driver-adapter.kicad_pcb, dc-motor-driver-adapter.kicad_sch]
2024-04-10 Плата замовлена.
    [dc-motor-driver-adapter.kicad_pcb]
2024-04-30 Програму будемо писати прям тут.
2024-05-11 О. Шось скомпілював і навіть прошив, і все, бляха, працює.
2024-05-11 О, додав UART на 115200. Поки використовую для відлагодження.
2024-05-11 UART замінен на Debug. TX only.
2024-05-11 Шось воно незрозуміло якось працює. Нахрін с пляжа.
2024-05-11 Хрін знає як працює капче. Спробую переробити на просто таймер та переривання.
2024-05-11 Почистив від зайвого коду.
2024-05-27 Тестова реалізація CRSF.
2024-05-27 Ревізія два - мега-спрощена.
    [dc-motor-driver-adapter.csv, dc-motor-driver-adapter.kicad_pcb, dc-motor-driver-adapter.kicad_sch]
2024-06-16 Починаю працювати над I2C DAC.
    [dc-motor-driver-adapter.csv, dc-motor-driver-adapter.kicad_pcb, dc-motor-driver-adapter.kicad_sch]
2024-06-17 Начебто повинно працювати. Поїду подивклюсь як воно себе веде на тачці.
2024-06-24 Збереження.
2024-06-25 Додан таймаут для приймача.
2024-07-10 Додана підтримка VESC-контроллерів через ADC вхід.
2024-08-13 Сгенеровані хекси для лівого та правого борта. Та хекс для лебідки.
